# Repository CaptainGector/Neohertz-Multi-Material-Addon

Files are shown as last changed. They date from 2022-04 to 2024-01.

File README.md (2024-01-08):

# A Rotary Multi-Material Addon for Your 3D Printer
A WIP Multi-Material Upgrade designed to be simpler, easier to build, and more reliable. The models are developed in FreeCAD and I've been testing with printers running Klipper firmware. 

**The sell**: Have you SEEN how much work it is to assemble the linear MMUs? Have you _seen_ the mess of filament they spit out backwards? And their solution to the spagetti is to build _yet another_ complicated mechanism to keep the slack filament under control! What if there was an easier way? What if there was a sleek, straightforward, compact, easy to assembly, easy to maintain, no-nonsense multi-material addon for any 3d printer? The printer never stops, all the firmware is extremely straightforward, the tolerances are low, the electronics are simple, it can easily be mounted in a small space, the bill of materials is short and cheap, it's easy to manufacture out of metal, what more could you want? 

- Few parts counts (Only 3 bearings, no linear rails)
- Fast assembly, there are only 3 major components to the build.
- Way more compact than any other multi-material system
- Handles way more filament paths than any other multi-material system
- Doesn't require additional hardware such as a filament-rewinder or special filament enclosure

# More details
A filament strand only engages with the feed gear when the cam bearing allows the spring-tensioned lever to sink and engage. Once this happens, the feed motor can quickly feed the filament either way. This removes the need for a fancy magnetic or gated solution to prevent accidental filament feeding. This may even work as an extruder by itself, replacing an existing bowden setup.

The two actuators are mounted on a frame capable of rotating around the filament pathways. Or, the actuators could be held in place and the filament runs could be rotated. I think wire management will be easier than managing the filament wrapping around itself. I don't think going around 360+ degrees is a good idea, the wires would wrap up, it should be limited to only rotate once, ~350degrees. 

# Status
Right now (as of August, 6th, 2023), I've gotten the basic prototype build working as a standalone device. I have not yet completed a test print because I'm still having issues with reliablility. Notably, I was having the carousel stepper skip steps while trying to cut the filament. The gearing ratio has been improved to help with that, but I haven't tested that yet. The filament feed mechanism needs to be pulled with like four springs in order for it to feed filament even sort of reliably, though I can work around this for the most part. The biggest issue is when the filament is sliced and then it tries to feed new filament into the exit tube; the filament often gets caught in the pneumatic fitting or the print itself. Will need to embed a bowden tube into the print to help with this. Hopefully with the most recent changes, the unit will be reilable enough to start test printing. I still have to figure out slicer settings, but I can just add a klipper macro GCODE for filament changes when I get there. 

### Firmware
I exclusively use klipper with my printers, and it has some nice utilities to set this up. I have a second motherboard dedicated to just running the MMU and klipper has it attached as a secondary MCU. I use 'MANUAL_STEPPER' for the carousel/magazine stepper and a second extruder motor instance for the feed stepper. The feed stepper can be syncronized with the primary extruder stepper for normal operation, and then made indepentant when feeding forward new filament after the old filament is sliced. To perfectly optimize this process, it would probably require writing some python code and a subroutine in klipper, but using the existing tools seems to work just fine. I have a couple macros in my testing setup for each action the MMU can take. 

The modified klipper firmware would be useful for features like automatically preventing filament tangles (instead of just rotating around constantly and wrapping up the filaments). It would also be good for splicing in new filament without interrupting a print, so the print head would always keep moving (it may need to pause for a fraction of a second while the filament is sliced). It would probably also be useful for automatically adjusting print parameters for individual filaments, and other more advanced utilities. 

## TODO
- ~~Change gears to printable gears~~
- ~~Add spring mounting point~~
- Reinforce lever arm (a lot)
- ~~Add filament exit to pivot frame~~
- ~~Finish filament paths~~
- ~~Add filament knife to pivot frame(?)~~
(06/10/23)
- Big carousel gear needs to be keyed to shaft
- Switch to better filament feed gear (why is amazon full of just really terrible feed gears?)
- Improve printability of exit funnel
- Re-design lever for more leverage and less twisting (move pivot point inline with cam bearing)
- Develop better klipper integration
- TEST PRINT!
- Add homing switch
- Add optional full-rotaton stop to prevent filament tangles (might be one in the same with a the homing switch)
- Include mounting point options on the pivot frame
- Investigate better filament feeding mechanism; for direct bowden printing. (Needs larger carousel)
- Improve printability of all parts for final deployment of Version 1.
- Finalize prototype BOM

<a href="https://bmc.link/zackwhitlock" target="_blank">Buy Me A Coffee</a>

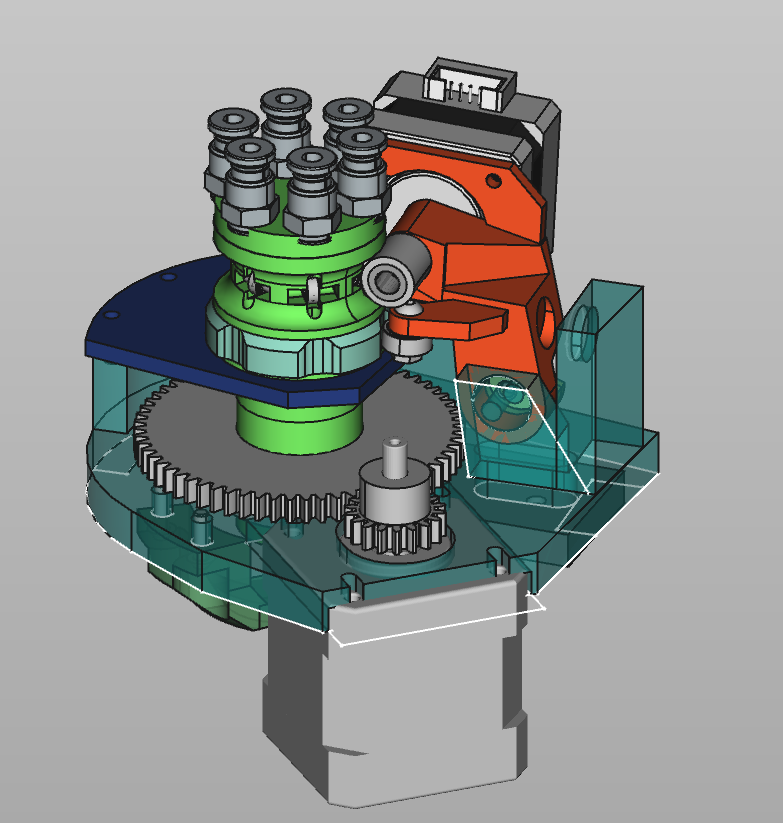
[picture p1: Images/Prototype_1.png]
Mockup Image

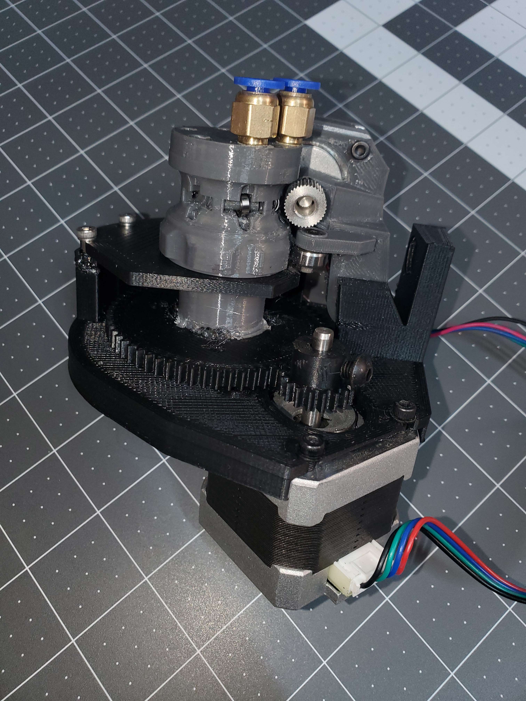
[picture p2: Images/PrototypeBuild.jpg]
Build Image


### Other names/tags/search terms
Filament carousel, rotating MMU, no slide MMU, multi-material mod.

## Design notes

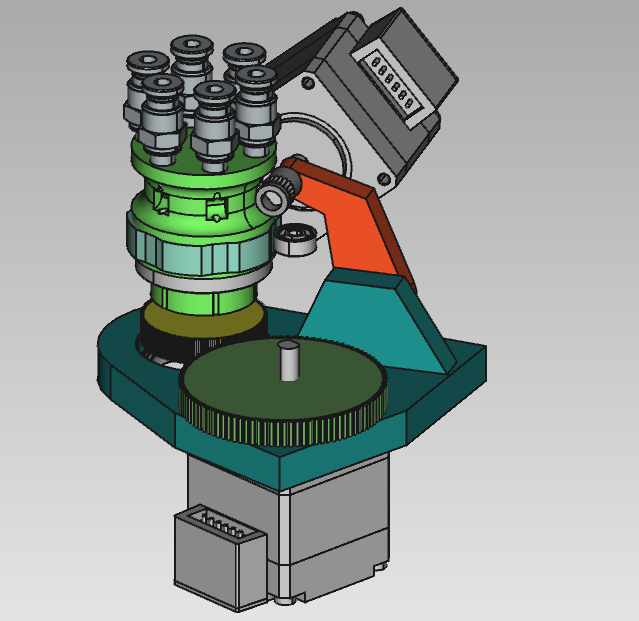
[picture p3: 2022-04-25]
Images/IMG_Mockup.png

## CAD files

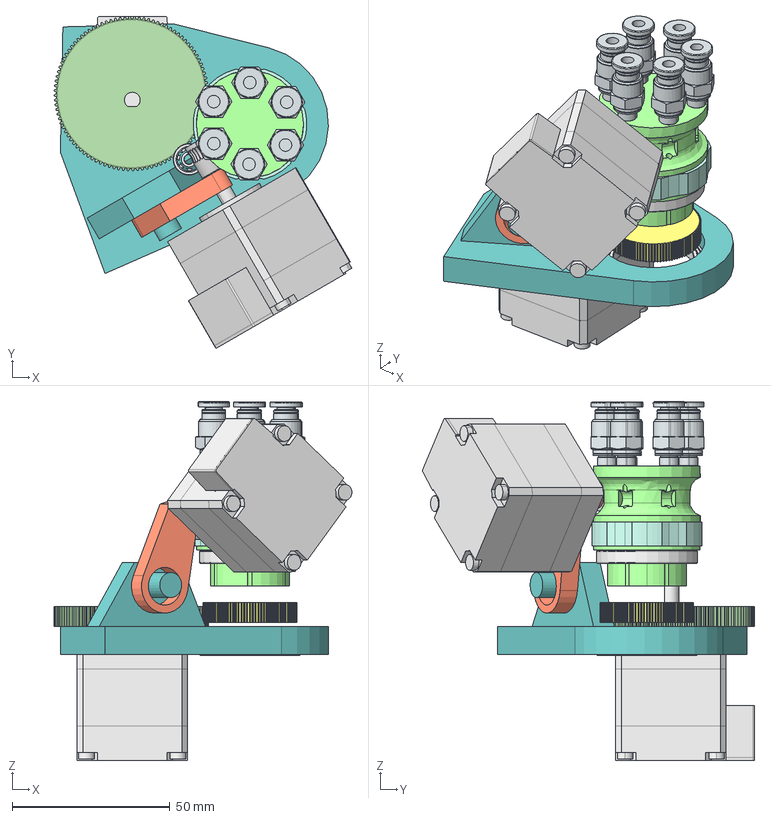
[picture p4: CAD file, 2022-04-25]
MMU.FCStd
94.4 x 105.3 x 113.9 mm
Chambers
RotateTeeth
SelectorBumps
Lever
Hobbed Shaft
MotorFeed
PivotFrame
MotorTurn
TurnGear
pc4-m6
pc4-m007
pc4-m008
pc4-m009
pc4-m010
pc4-m011
